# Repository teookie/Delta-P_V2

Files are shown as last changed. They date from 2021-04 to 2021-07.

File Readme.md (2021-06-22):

Delta-P V2

Custom Extruder for MK3 3D printer
- Dragon hotend only
- MMU2 only (or run w/o runout sensor)
- requires custom firmware or custom sensor. see: https://www.prusaprinters.org/prints/3091-delta-p-extruder
- you will need to send the following gcode commands to calibrate for the gear reduction:
```
M350 E16
M92 E415
M500
```

These files are currently in development. Don't expect everything to be perfect.

June 21, 2021  
added:  
brace_stock_frame  
clamp_stock_frame

renamed:  
brace --> brace_bear_frame  
clamp --> clamp_bear_frame

Updated toolholder to allow sensor connector to plug into the back of the sensor. Requires soldering the 3 pin header on the other side of the pcb. Improves wire routing.

April 18, 2021
Created repo and uploaded files

May 12, 2021
Fixed reduced x build volume. should pass self check now.
- Moved fan fwd so it no longer contacts x carriage during auto home
- Trimmed back cable management guides on carriage
- Modified pinda clamp

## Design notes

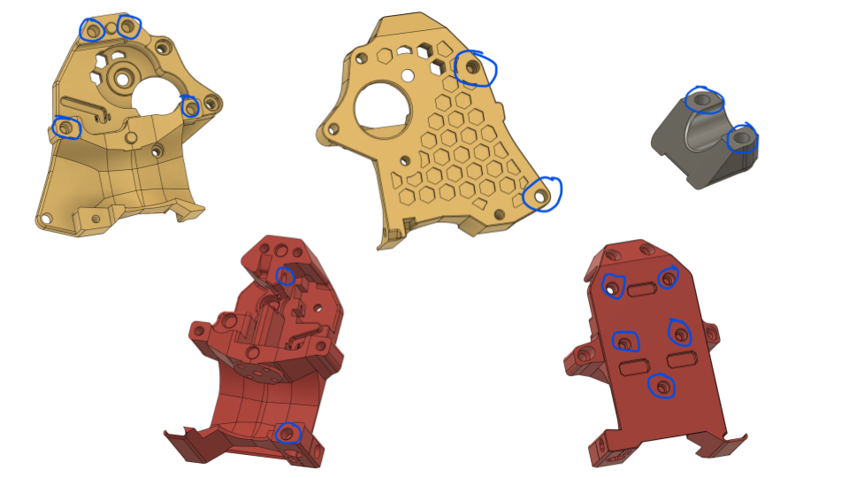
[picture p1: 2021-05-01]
heatsert_locations.png

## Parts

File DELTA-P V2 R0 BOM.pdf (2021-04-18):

Link to DELTA-P V2 R0 CAD: https://a360.co/319Luvu

item | qty | note
M3 heatset inserts | | 18 M3 X D5.0 X L4.0 https://www.aliexpress.com/item/4000232858343.html?spm=a2g0s.9042311.0.0.79444c4d26AtRT
M2 x 8 SHCS | 1
M3 x 8 SHCS | 4
M3 x 10 SHCS | 4
M3 x 12 SHCS | 2
M3 x 12 FHCS | 1
M3 x 16 SHCS | 3
M3 x 18 SHCS | 6
M3 x 20 SHCS | 2
M3 x 40 SHCS | 1
M3 square nut | 1
M3 locknut | 1
M3 x 25 smooth shaft | 1
spring | | 1 from a ballpoint pen (approx 4.18 OD, 3.4 ID, 16.25 long)
Bondtech Drivegears | | 1 https://www.filastruder.com/collections/bondtech/products/drivegear-kit?variant=12119190634567
thumbscrew | | 1 https://www.filastruder.com/collections/bondtech/products/bondtech-thumbscrew-assembly
shaft / idler | | 1 https://www.filastruder.com/collections/bondtech/products/bondtech-shaft-gear-assembly
motor gear | | 1 https://www.filastruder.com/collections/bondtech/products/bondtech-motor-gear
MR85 bearing | | 2 https://www.amazon.com/gp/product/B082PQ6T21/ref=ppx_yo_dt_b_asin_title_o02_s00?ie=UTF8&psc=1
inverted IR sensor | | 1 https://easyeda.com/teookie/inverted-ir-sensor
pass through PTFE fitting | | 1 https://www.amazon.com/gp/product/B01IB81IHG/ref=ppx_yo_dt_b_search_asin_title?ie=UTF8&psc=1

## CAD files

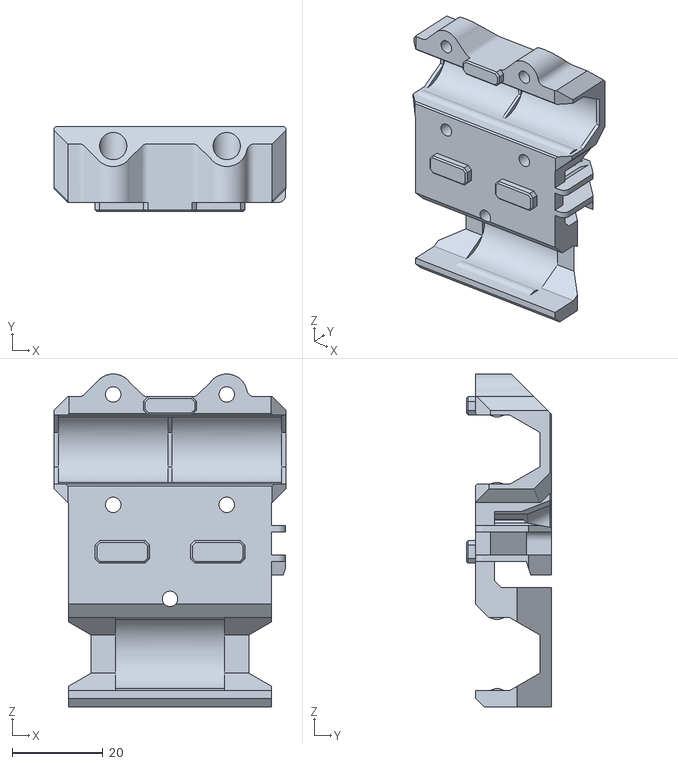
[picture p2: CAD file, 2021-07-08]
carriage_stock_frame.stl
51.0 x 18.8 x 73.3

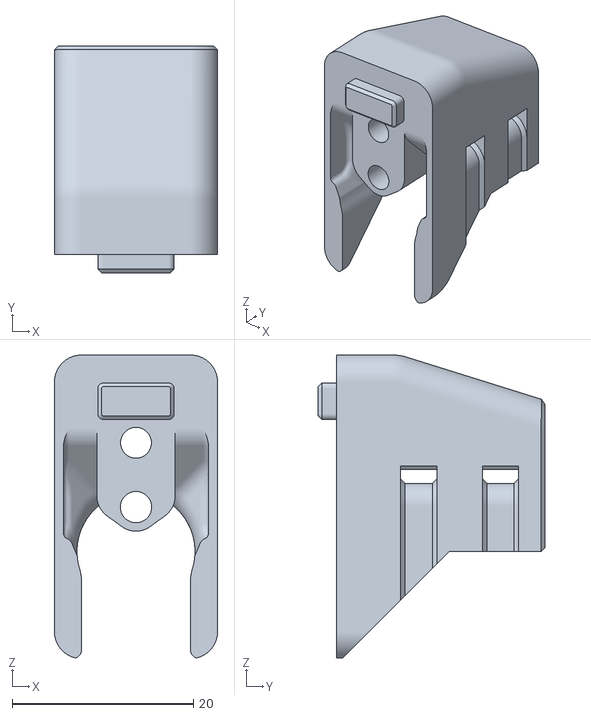
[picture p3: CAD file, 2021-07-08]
brace_stock_frame.stl
18.0 x 25.0 x 33.4

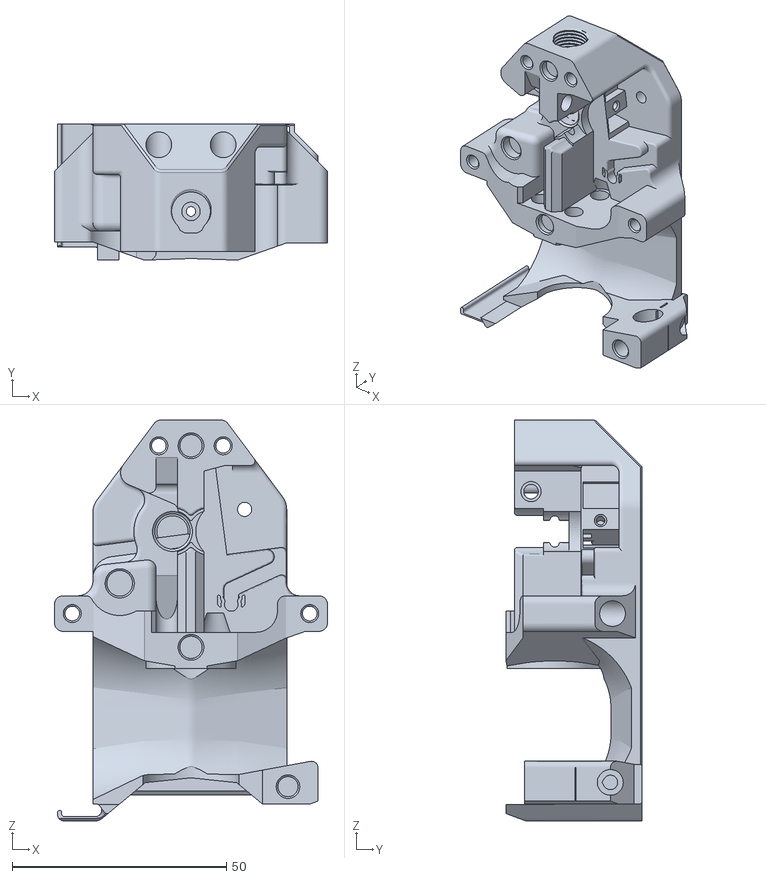
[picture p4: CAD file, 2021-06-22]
toolholder.stl
63.7 x 31.8 x 93.5

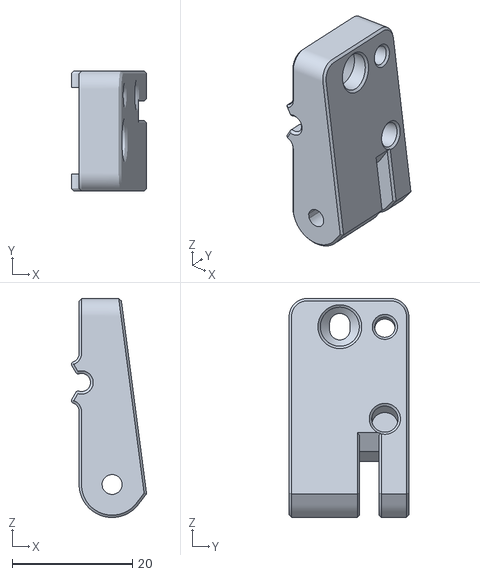
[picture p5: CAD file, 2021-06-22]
arm.stl
12.5 x 20.0 x 36.5

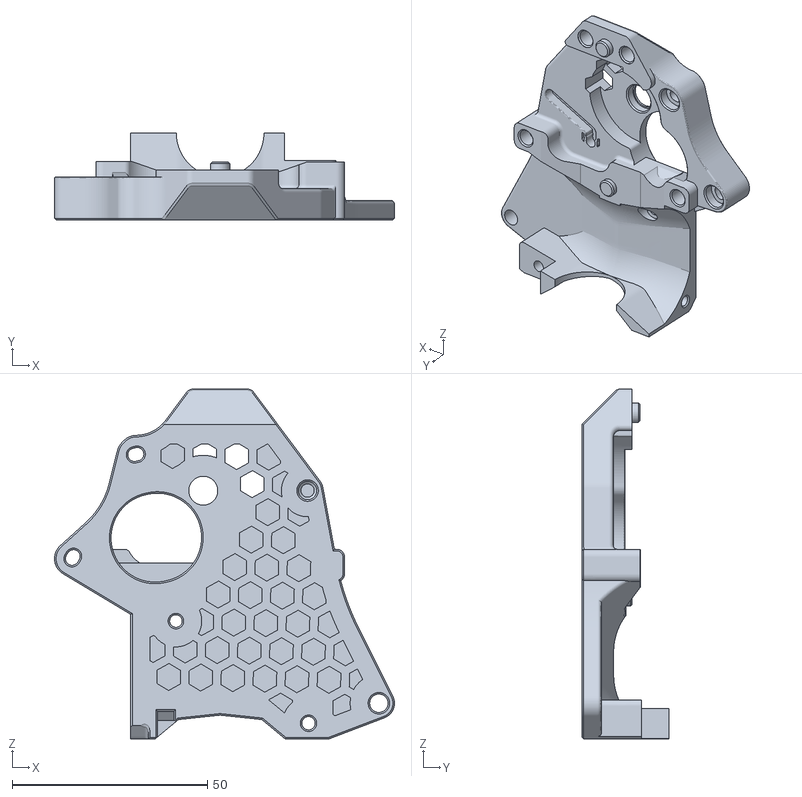
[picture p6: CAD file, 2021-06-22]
cover.stl
87.0 x 22.2 x 89.5

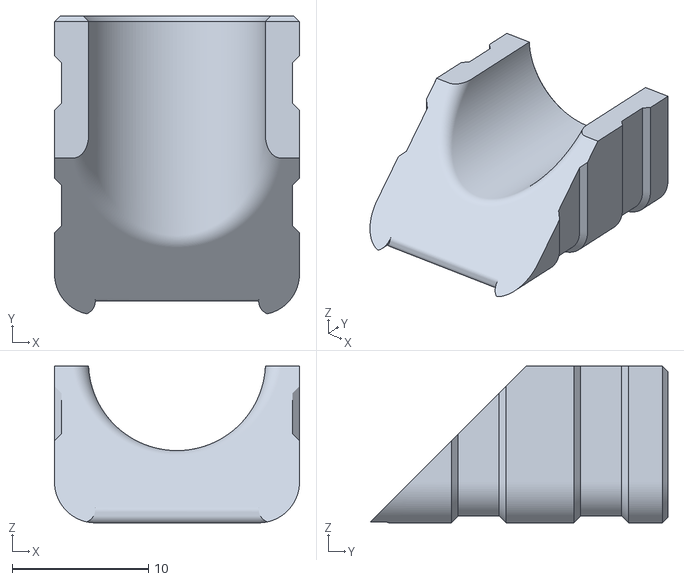
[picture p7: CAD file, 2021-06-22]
clamp_stock_frame.stl
18.0 x 21.9 x 11.5

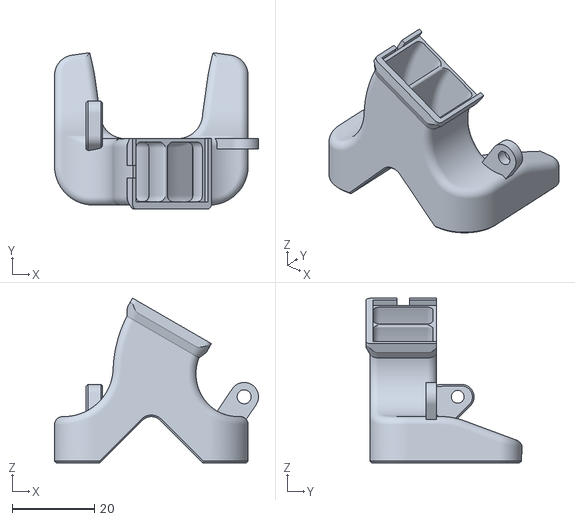
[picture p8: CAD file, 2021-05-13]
ductV2R2.stl
49.7 x 38.1 x 40.2

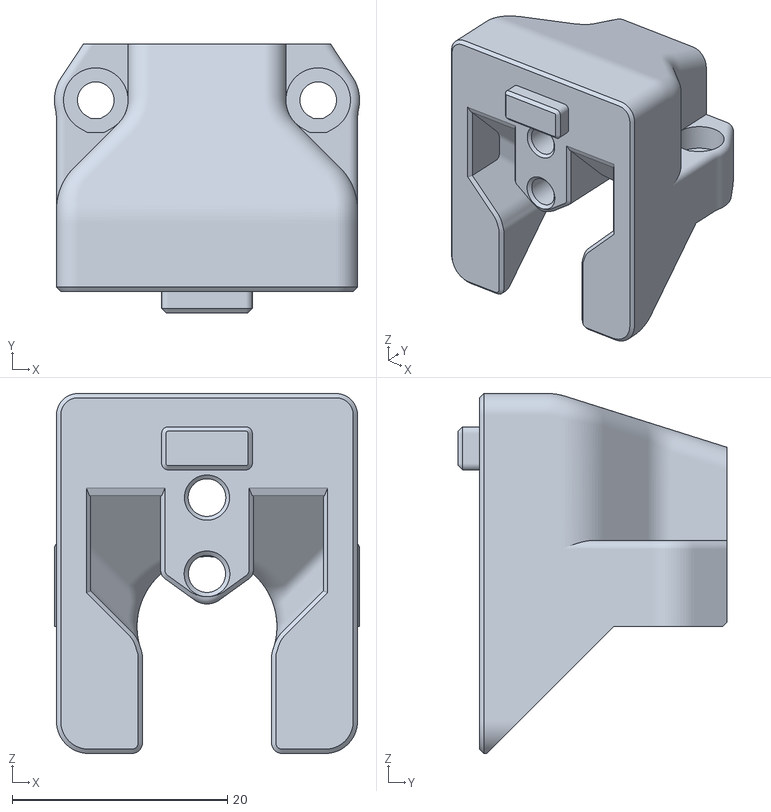
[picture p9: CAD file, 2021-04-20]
brace_bear_frame.stl
28.4 x 25.0 x 33.5

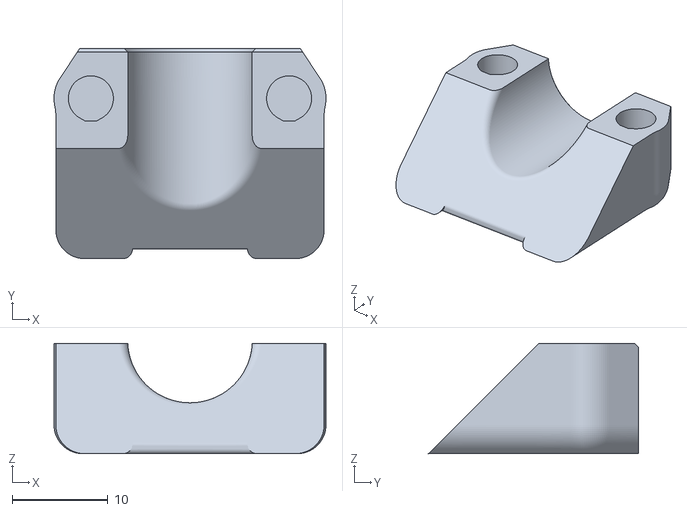
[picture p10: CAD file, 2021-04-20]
clamp_bear_frame.stl
28.4 x 21.9 x 11.5

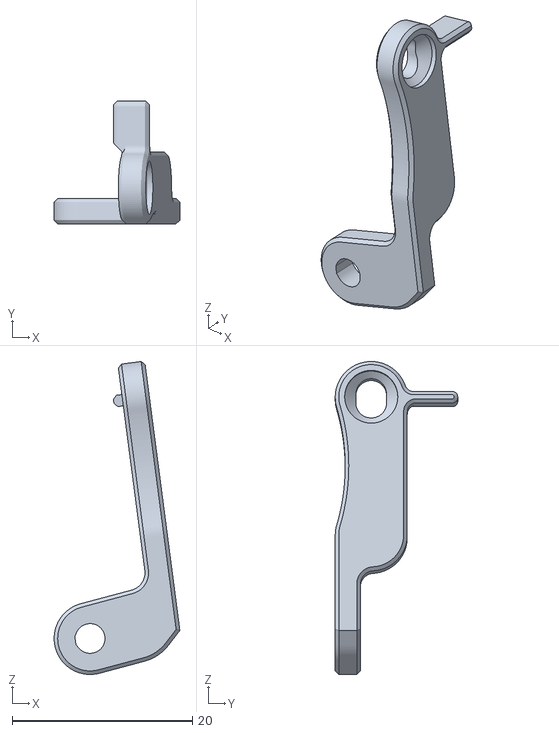
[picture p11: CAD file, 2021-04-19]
lever.stl
14.0 x 13.6 x 34.8

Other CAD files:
carriage.stl

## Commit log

2021-04-18 deleted files added by accident
    [new_z_tops_left.stl, new_z_tops_right.stl]
2021-04-19 added groove to cover and toolholder
    [cover.stl, toolholder.stl]
2021-04-19 added 45deg chamfer to arm & lever
    [arm.stl, lever.stl]
2021-04-20 improved cable management
    [arm.stl, brace.stl, carriage.stl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]
2021-04-21 carriage and toolholder updates
    [carriage.stl, toolholder.stl]
2021-04-21 enlarged motor wire channel on toolholder
    [toolholder.stl]
2021-05-01 added heatsert location image
2021-05-13 added 10mm x travel by moving fan and cable guides
    [cover.stl, ductV2R2.stl, toolholder.stl]
2021-05-13 forgot carriage.stl on last push...
    [carriage.stl]
2021-06-22 added clamp and brace for stock frame
    [arm.stl, brace_bear_frame.stl, brace_stock_frame.stl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]
2021-06-22 updated toolholder
    [toolholder.stl]
2021-07-08 carriage_stock_frame updates
    [brace_stock_frame.stl, carriage_stock_frame.stl]
